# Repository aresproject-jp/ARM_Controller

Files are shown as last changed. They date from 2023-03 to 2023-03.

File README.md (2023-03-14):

# ARM Controller
2023年の2~3月あたりにアームまわりの電装を開発してた[藤田](https://twitter.com/771_8bit)です。

## 全体像
Jetson Nanoからアームを制御するための電装です。

* 通信には拡張性のためにCANを使う
    * Jetson NanoからCANコントローラMCP2515を扱うのは面倒なため、Seeeduino XIAOを介してCANを扱う
    * Jetson Nanoに直接MCP2515を接続するためにデバイスドライバをいじるのがかなりダルかった
* アームの制御はArduino Megaで行う
    * モーターとエンコーダとスイッチとそれなりにピン数がほしいのでMegaかDue
    * ロータリエンコーダの電圧が5VだからMegaがいい
    * DueにはCANコントローラが内蔵されてるけど、JetsonでもArduino経由でMCP2515を使うからMegaからMCP2515を使ったほうが結局楽
    * ハイスペックなマイコンが必要なわけでもないのでMegaでいい
* サーボモータ1つとDCモーター5つを制御する
    * DCモーターのモータードライバは[MD10C R3](https://www.cytron.io/p-10amp-5v-30v-dc-motor-driver)
    * サーボモータは[DS5160](https://www.amazon.co.jp/dp/B07XBYKB65)
    * DCモーター1つにロータリエンコーダとリミットスイッチが1つずつ(ロータリエンコーダは減らすかも)

```mermaid
flowchart TD
    J(fa:fa-microchip Jetson Nano)<-->|USB| S(fa:fa-microchip Seeeduino XIAO   fa:fa-code CAN_USB)
    S <-->|SPI| M1[MCP2515]
    M1<-->|CAN| M2[MCP2515]
    M2<-->|SPI| M(fa:fa-microchip Arduino Mega fa:fa-code ARM_unit_MEGA)

    M<-->RE[E6A2-CW3C]
    M<-->MD[MD10C]
    M<-->RS[Limit Switch]
```
<!--https://mermaid.live/edit-->

## CAN
CAN通信はController Area Networkの略で、もとは自動車内の通信用です。差動伝送のペアの信号線にノードを接続する多対多の通信規格です。送信時はデータの種類を示してデータを垂れ流して受信時は欲しいデータを受け取るだけで、全てをコントロールするマスターはありません。通信相手を指定するのではなく通信内容を指定するのがCANの特徴です。差動伝送であるため電気的なノイズに強く、CRCによる誤り検出も備えていて信頼性の高い規格です。

標準フォーマットのCANでは、11bitのIDをつけて最大8byteのデータをやりとりできます。ここでは**uint32_tのデータ**を1つ送るために4byteのデータを送受信します。

### CANハードウェア
ArduinoでCAN通信を行うには、[MCP2515](https://akizukidenshi.com/catalog/g/gI-12030/)というCANコントローラと、[MCP2562](https://akizukidenshi.com/catalog/g/gI-14383/)というCANトランシーバーを使います。CANコントローラがSPIからCANに変換し、CANトランシーバーが差動通信に変換します。2つのICが一体になった[MCP25625](https://akizukidenshi.com/catalog/g/gI-12663/)もありますが、表面実装のパッケージしかないのでARESではMCP2515とMCP2562を使います。

回路図は以下の通りです。MCP2562のSLEEPはLOWにする必要があります。VCCはSeeeduino XIAOなら3.3V、Arduino Megaなら5Vです。
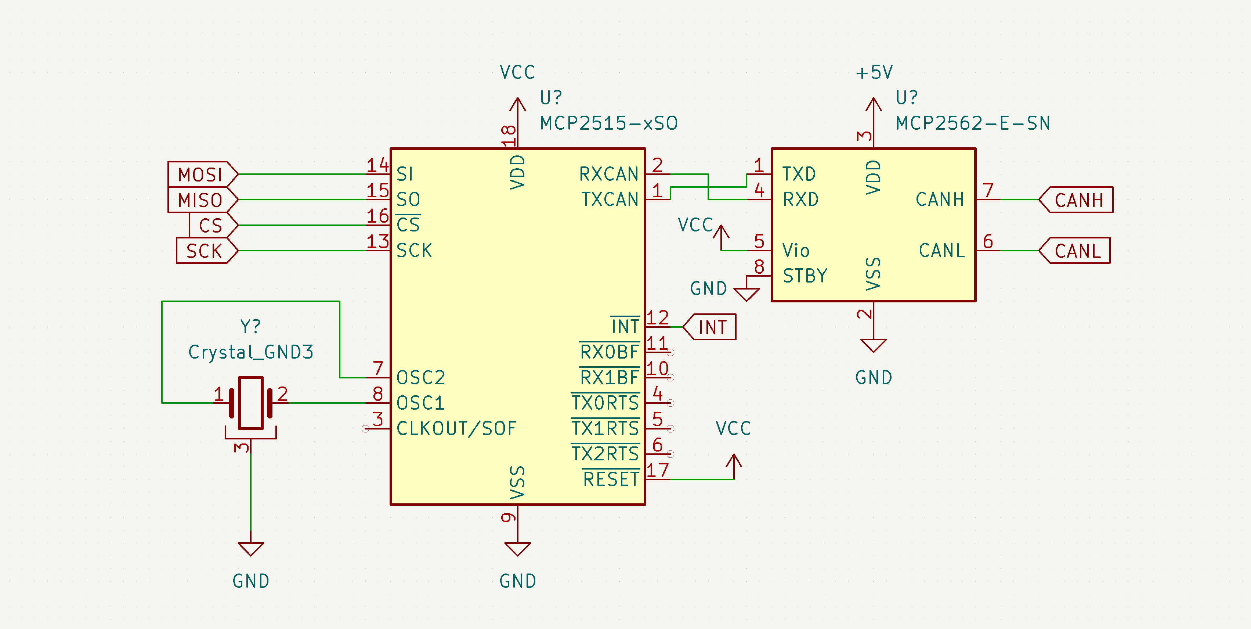
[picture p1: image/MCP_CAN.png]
MCP_CAN


### CANソフトウェア
ライブラリは[mcp_can](https://www.arduino.cc/reference/en/libraries/mcp_can/)を使います。```CAN_1000KBPS```として1Mbpsで通信します。

以下のような共用体を作り、CANのデータを格納します。```uint32_data```と```uint8_data```が同じメモリを共有し、CANで送信するuint8_tの配列にuint32_tのデータを変換します。

パディングを避けるため、```uint32_data```を先に定義します。

```cpp
typedef union
{
  uint32_t uint32_data;
  uint8_t uint8_data[4];
} msg_union;
msg_union msg = {0};
```

CANのIDの割り振りは以下の通りです。
|  ID  |  用途  |
| ---- | ---- |
|  0x100  |  サーボの角度指定  |
|  0x101  |  モーター1の速度指定  |
|  0x102  |  モーター2の速度指定  |
|  0x103  |  モーター3の速度指定  |
|  0x104  |  モーター4の速度指定  |
|  0x105  |  モーター5の速度指定  |
|  0x201  |  モーター1の角度取得  |
|  0x202  |  モーター2の角度取得  |
|  0x203  |  モーター3の角度取得  |
|  0x204  |  モーター4の角度取得  |
|  0x205  |  モーター5の角度取得  |
* サーボの角度指定
    * 送信した値がServo.write()の引数になる。単位は度。
* モーターの速度指定
    * 範囲は0-511で256で停止、その前後で正転逆転。
* モーターの角度取得
    * ロータリエンコーダの値の絶対値。
### CAN USB変換
Seeeduino XIAOを使ってJetson NanoからのUSBをCANに変換します。ここでCANに変換することで、足回りやアーム、バイオの機構にもCANを使うことができます。

送信フォーマットは以下の通りです。CANから受信した時も同じフォーマットでからUSBに送られます。
```
id(16進数表記),数値(10進数uint32_t)\n
```

Jetsonからは、```pip install pyserial```でインストールして、以下のコードで送信します。
```python
import serial

%デバイス名は変わるかも
_serial = serial.Serial("/dev/ttyACM0")
_serial.baudrate = 115200

%毎回の送信はこれだけ
_serial.write("101,300\n")
```

## モータードライバ
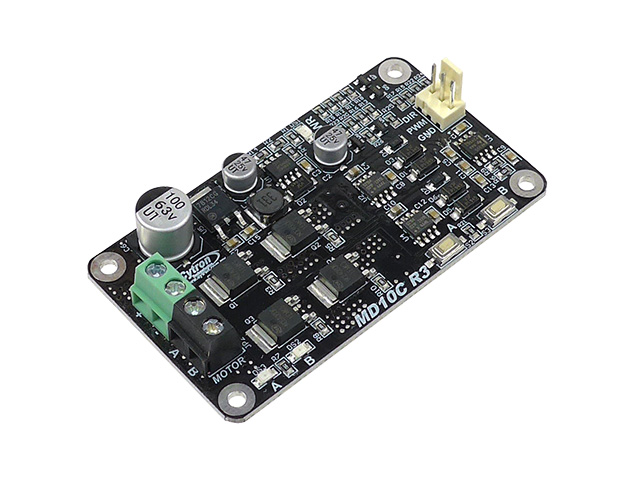
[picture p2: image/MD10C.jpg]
MD10C


* モータードライバ[MD10C R3](https://www.cytron.io/p-10amp-5v-30v-dc-motor-driver)の仕様
    * PWMピンで速度を、DIRピンで回転方向を制御する
    * PWM・DIRピンの電圧は3.3Vでも5Vでも問題ない
    * PWMの周波数がそのままモーターのスイッチング周波数になる

* [メーカー公式のライブラリ](https://www.arduino.cc/reference/en/libraries/cytron-motor-drivers-library/)の仕様
    * MD10Cは```PWM_DIR```を使う
    * ライブラリには```setSpeed```で-255~255の値を渡す
    * PWM出力は内部で[analogWrite](https://github.com/CytronTechnologies/CytronMotorDriver/blob/master/CytronMotorDriver.cpp#L29)を使ってる

## リミットスイッチ
* ただのマイクロスイッチで、マイコンで内蔵プルアップする

## ロータリエンコーダ
* [ライブラリ](https://www.arduino.cc/reference/en/libraries/encoder/)の仕様
    * [ドキュメント](https://www.pjrc.com/teensy/td_libs_Encoder.html)がそれなりに詳しい
    * 割込ピン(2,3,18,19,20,21)を優先的に使う
    * 他のピンを使うと```read()```を呼び出したときだけ[ピンの状態を読み取る](https://www.pjrc.com/teensy/td_libs_Encoder.html#polling)
* ソフトの仕様
    * タイマ割り込みで100Hzでロータリエンコーダの値をCANに送信する
    * 割込ピンでないピンはloop内で```read()```を呼び出す
    * リミットスイッチが押されたときはエンコーダの値を0にする
    * 値は絶対値をとって送信する

## サーボモータ
サーボモータの角度の初期値は以下のように指定しています。
```cpp
#define SERVO_default 90
```
## Megaのピン割当
タイマ割当に関しては[これ](https://qiita.com/srs/items/68981b6e695e6f4468ff)を参考にしました。

|  タイマ  |  用途  |
| ---- | ---- |
|  timer0  |  時間関数(delay,millis)  |
|  timer1  |  PWM(11,12)  |
|  timer2  |  未使用  |
|  timer3  |  [タイマ割り込み](https://qiita.com/GANTZ/items/1ae1797878bd7cefce7e)  |
|  timer4  |  PWM(6,7,8)  |
|  timer5  |  Servo.h  |

[Megaのピン配置詳細](https://content.arduino.cc/assets/Pinout-Mega2560rev3_latest.pdf)

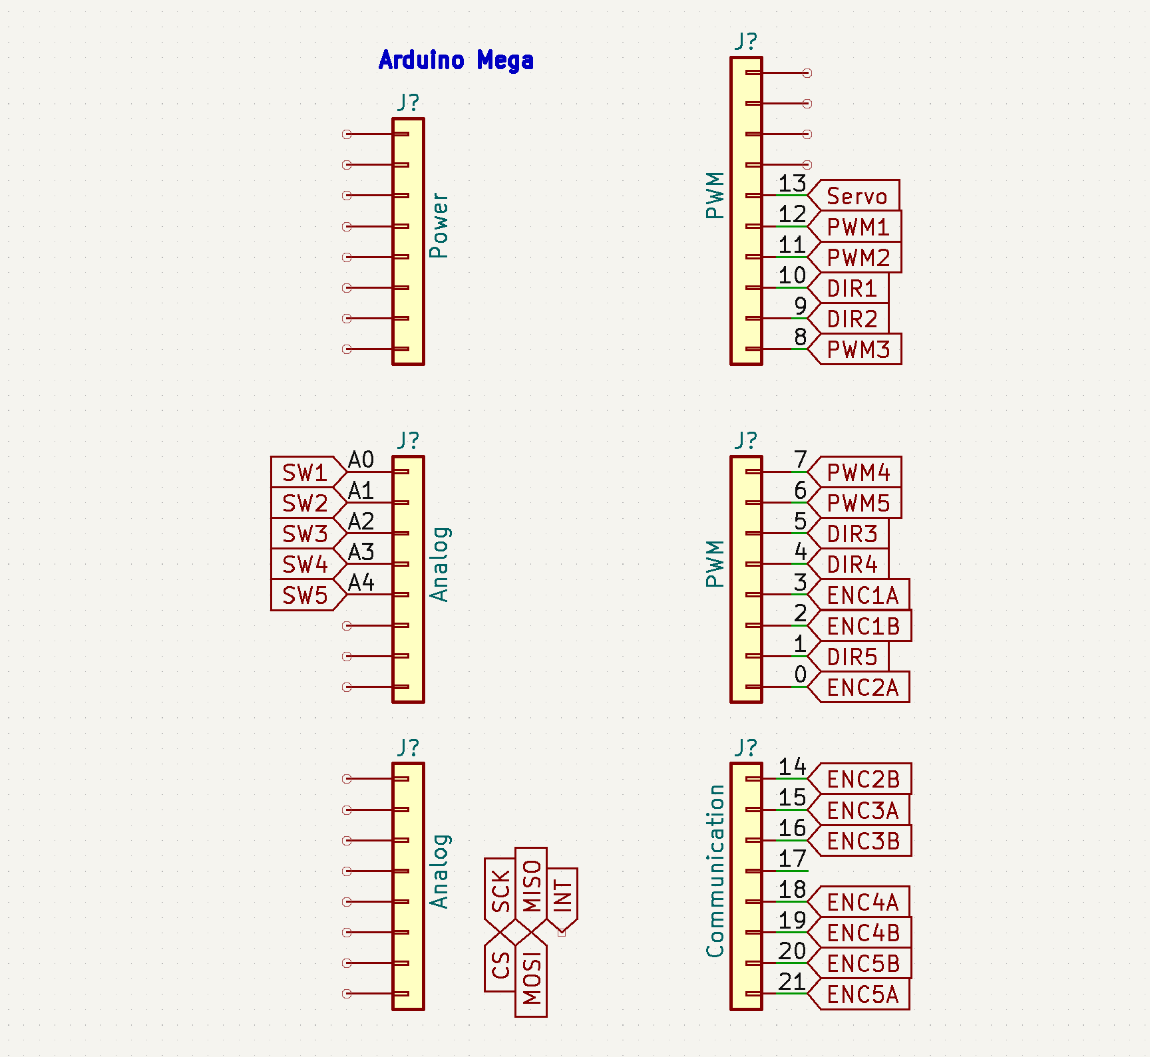
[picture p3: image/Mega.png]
Mega


## プロトタイプ基板
Prototype

サーボピン配置(左から)
* GND
* VCC
* PWM

エンコーダピン配置(上から)
* A
* B
* 5V
* GND

## ToDo
今は最低限の機能だけ実装しています。本来は以下の機能が必要です。
* 起動時にリミットスイッチにあてて原点復帰を行う
* ロータリエンコーダの値から、動作範囲を超えて動かないようにする
* ロータリエンコーダの値を分かりやすい単位にする

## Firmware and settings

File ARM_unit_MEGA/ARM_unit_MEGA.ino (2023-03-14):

// ARM unit for Arduino Mega
// kazuki fujita @771_8bit

#include <TimerThree.h>
bool timer_100Hz = false;

#include <mcp_can.h>
#include <SPI.h>
MCP_CAN CAN(53); // Set CS to pin 53
#define CAN_INT 48
typedef union
{
  uint32_t uint32_data;
  uint8_t uint8_data[4];
} msg_union;
msg_union msg = {0};

#include <Servo.h>
Servo servo;
#define SERVO_PWM 13
#define SERVO_default 90

#include "CytronMotorDriver.h"
//CytronMD motor(PWM_DIR, PWM, DIR);
CytronMD motor1(PWM_DIR, 12, 10);
CytronMD motor2(PWM_DIR, 11, 9);
CytronMD motor3(PWM_DIR, 8, 5);
CytronMD motor4(PWM_DIR, 7, 4);
CytronMD motor5(PWM_DIR, 6, 1);

#include <Encoder.h>
Encoder encoder1(3, 2);
Encoder encoder2(0, 14);
Encoder encoder3(15, 16);
Encoder encoder4(18, 19);
Encoder encoder5(21, 20);
//https://www.pjrc.com/teensy/td_libs_Encoder.html

#define SW1 A0
#define SW2 A1
#define SW3 A2
#define SW4 A3
#define SW5 A4

void send_CAN(uint32_t id, uint32_t data) {
  msg.uint32_data = data;
  byte sndStat = CAN.sendMsgBuf(id, 0, 4, msg.uint8_data);
  /*
    if (sndStat == CAN_OK) {
    //Serial.println("Message Sent Successfully!");
    } else {
    //Serial.println("Error Sending Message...");
    }
  */
  delayMicroseconds(100);
}

void ISR_100Hz() {
  if (timer_100Hz) {
    //Serial.println("100Hz overrun");
  } else {
    timer_100Hz = true;
  }
}

void setup() {
  //Serial.begin(115200);

  pinMode(CAN_INT, INPUT);
  if (CAN.begin(MCP_ANY, CAN_1000KBPS, MCP_16MHZ) == CAN_OK) {
    //Serial.println("MCP2515 Initialized Successfully!");
  }
  else {
    //Serial.println("Error Initializing MCP2515...");
  }
  CAN.setMode(MCP_NORMAL);

  servo.attach(SERVO_PWM);
  servo.write(SERVO_default);

  pinMode(SW1, INPUT_PULLUP);
  pinMode(SW2, INPUT_PULLUP);
  pinMode(SW3, INPUT_PULLUP);
  pinMode(SW4, INPUT_PULLUP);
  pinMode(SW5, INPUT_PULLUP);

  Timer3.initialize(10000);
  Timer3.attachInterrupt(ISR_100Hz);
}

void loop() {
  if (timer_100Hz) {
    timer_100Hz = false;
    
    //Serial.println("100Hz");
    send_CAN(0x201, abs(encoder1.read()));
    send_CAN(0x202, abs(encoder2.read()));
    send_CAN(0x203, abs(encoder3.read()));
    send_CAN(0x204, abs(encoder4.read()));
    send_CAN(0x205, abs(encoder5.read()));
    if (digitalRead(SW1) == LOW) {
      encoder1.write(0);
    }
    if (digitalRead(SW2) == LOW) {
      encoder2.write(0);
    }
    if (digitalRead(SW3) == LOW) {
      encoder3.write(0);
    }
    if (digitalRead(SW4) == LOW) {
      encoder4.write(0);
    }
    if (digitalRead(SW5) == LOW) {
      encoder5.write(0);
    }
  }

  if (!digitalRead(CAN_INT))
  {
    long unsigned int rxId;
    unsigned char len = 0;
    CAN.readMsgBuf(&rxId, &len, msg.uint8_data);

    //Serial.print(rxId, HEX);
    //Serial.print(",");
    //Serial.println(msg.uint32_data);

    switch (rxId) {
      case 0x100:
        servo.write(msg.uint32_data);
        break;
      case 0x101:
        motor1.setSpeed((int)msg.uint32_data - 256);
        break;
      case 0x102:
        motor2.setSpeed((int)msg.uint32_data - 256);
        break;
      case 0x103:
        motor3.setSpeed((int)msg.uint32_data - 256);
        break;
      case 0x104:
        motor4.setSpeed((int)msg.uint32_data - 256);
        break;
      case 0x105:
        motor5.setSpeed((int)msg.uint32_data - 256);
        break;
      default:
        break;
    }
  }
  encoder2.read();
  encoder3.read();
}

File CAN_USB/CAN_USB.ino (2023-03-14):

// CAN_USB for Seeeduino XIAO
// kazuki fujita @771_8bit

#include <mcp_can.h>
#include <SPI.h>

MCP_CAN CAN(6); // Set CS to pin 6
#define CAN_INT 7

void setup()
{
  pinMode(CAN_INT, INPUT);
  Serial.begin(115200);

  if (CAN.begin(MCP_ANY, CAN_1000KBPS, MCP_16MHZ) == CAN_OK) {
    //Serial.println("MCP2515 Initialized Successfully!");
  }
  else {
    //Serial.println("Error Initializing MCP2515...");
  }
  CAN.setMode(MCP_NORMAL);   // Change to normal mode to allow messages to be transmitted
}


typedef union
{
  uint32_t uint32_data;
  uint8_t uint8_data[4];
} msg_union;
msg_union msg = {0};


int i = 0;
char buff[256];
uint32_t UART_data[16];
char *p;

void loop()
{
  if (!digitalRead(CAN_INT))                        // If CAN_INT pin is low, read receive buffer
  {
    long unsigned int rxId;
    unsigned char len = 0;
    CAN.readMsgBuf(&rxId, &len, msg.uint8_data);      // Read data: len = data length, buf = data byte(s)

    Serial.print(rxId, HEX);
    Serial.print(",");
    Serial.println(msg.uint32_data);
  }

  uint32_t canid = 0;
  int i_UART_data = 0;
  while (Serial.available() > 0) {
    buff[i] = (char)Serial.read();
    if (buff[i] == '\n') {
      buff[i] == '\0';
      canid = strtol(strtok(buff, ","), NULL, 16);

      for (i_UART_data = 0; true; i_UART_data++) {
        p = strtok(NULL, ",");
        if (p != NULL) {
          UART_data[i_UART_data] = atoi(p);
        } else {
          break;
        }
      }
      i = 0;
      break;
    } else {
      i += 1;
    }
  }
  if (i_UART_data > 0) {
    msg.uint32_data = UART_data[0];
    //Serial.println(canid);
    byte sndStat = CAN.sendMsgBuf(canid, 0, 4, msg.uint8_data);
    /*
        if (sndStat == CAN_OK) {
          Serial.println("Message Sent Successfully!");
        } else {
          Serial.println("Error Sending Message...");
        }
    */
    delayMicroseconds(500);
  }
}
